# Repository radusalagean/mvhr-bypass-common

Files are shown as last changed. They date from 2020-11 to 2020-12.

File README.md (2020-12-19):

# MVHR Bypass

IOT device able to control the [MVHR Summer Bypass](https://www.zehnder.co.uk/summer-bypass) based on inside and outside temperatures.

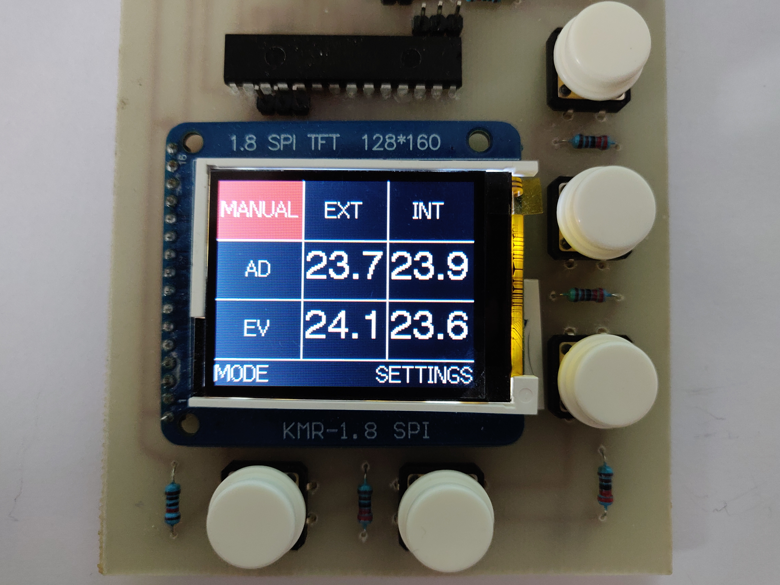
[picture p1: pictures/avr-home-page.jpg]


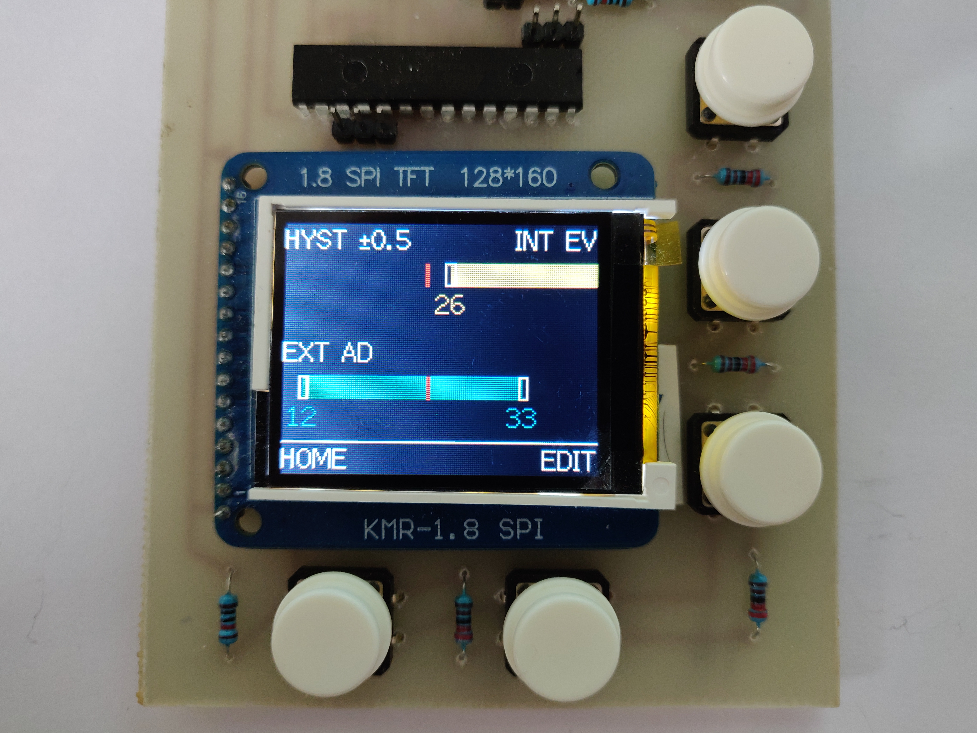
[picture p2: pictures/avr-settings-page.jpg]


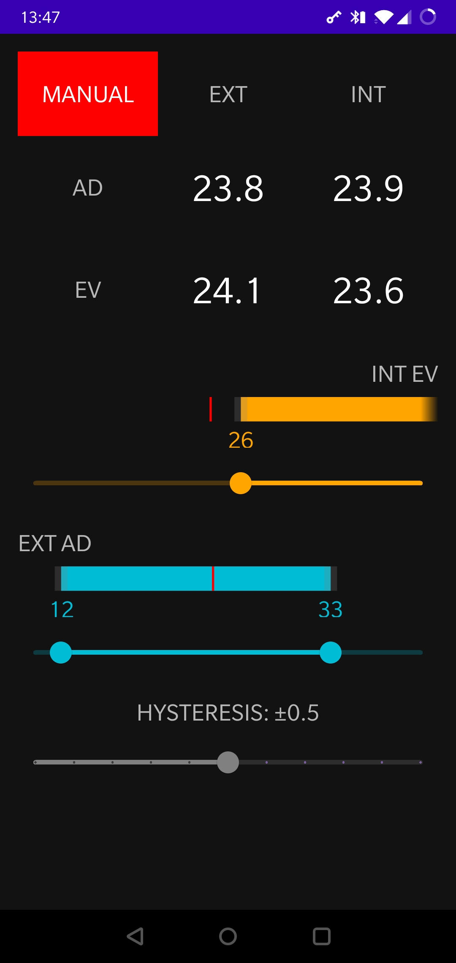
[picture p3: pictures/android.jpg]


## Compilation

Both the [**mvhr-bypass-arduino**](https://github.com/radusalagean/mvhr-bypass-arduino) and the [**mvhr-bypass-esp8266**](https://github.com/radusalagean/mvhr-bypass-esp8266) projects can be edited and compiled with **VSCode**, which needs the **Arduino IDE** installed and the following **VSCode plugins**:

- [Arduino](https://marketplace.visualstudio.com/items?itemName=vsciot-vscode.vscode-arduino)
- [C/C++](https://marketplace.visualstudio.com/items?itemName=ms-vscode.cpptools)

### Dependencies and versions

Check the **release notes** for each MVHR Bypass repo for the latest dependency versions known to work with that specific release.

In addition, the  **mvhr-bypass-arduino** project relies on the [**TFT_ILI9163**](https://github.com/radusalagean/TFT_ILI9163) library, which is included as a git submodule.

The **mvhr-bypass-common** repository contains code which is shared by both **mvhr-bypass-arduino** and **mvhr-bypass-esp8266** and is included in those repos as a git submodule.

### Software version compatibility

Add a new entry every time a new version is released. New releases go on top.

| [mvhr-bypass-arduino](https://github.com/radusalagean/mvhr-bypass-arduino) | [TFT_ILI9163](https://github.com/radusalagean/TFT_ILI9163) | [mvhr-bypass-esp8266](https://github.com/radusalagean/mvhr-bypass-esp8266) | [mvhr-bypass-common](https://github.com/radusalagean/mvhr-bypass-common) | [mvhr-bypass-android](https://github.com/radusalagean/mvhr-bypass-android) |
| --- | --- | --- | --- | --- |
| [1.0.0](https://github.com/radusalagean/mvhr-bypass-arduino/releases/tag/v1.0.0) | [1.0.0](https://github.com/radusalagean/TFT_ILI9163/releases/tag/v1.0.0) | [1.0.0](https://github.com/radusalagean/mvhr-bypass-esp8266/releases/tag/v1.0.0) | [1.0.0](https://github.com/radusalagean/mvhr-bypass-common/releases/tag/v1.0.0) | [1.0.0](https://github.com/radusalagean/mvhr-bypass-android/releases/tag/v1.0.0) |

### Flashing software updates on ATmega328p

Available options:

1. [Flashing with a **USB to Serial converter**](https://youtu.be/Sww1mek5rHU?t=1800)

1. Using an **Arduino board as an ISP**:

    - Write the **ArduinoISP** sketch which is included with Arduino IDE (located in File -> Examples -> ArduinoISP)

    - Hook up the Arduino Uno to the ATmega328p *(Double check the sketch in case these change in future versions)*:

    | Arduino Uno Pin | ATmega328p Pin |
    | --------------- | -------------- |
    | D10             | RST            |
    | D11             | D11            |
    | D12             | D12            |
    | D13             | D13            |
    - In VSCode, select the **Arduino as ISP** programmer and then run the **Arduino: Upload Using Programmer** command.

### Flashing software updates on ESP8266

Available options:

1. **OTA Update:**
   
   - Have the PC connected to the **same network** as ESP8266
   - In VSCode, in `arduino.json`, set the `port` value to the current IP address of the ESP8266
   - Upload
2. **Direct Serial Flashing:**
   
   - On the Arduino board, hook up the **RST** pin to **GND** (this bypasses the onboard microcontroller so you can use just the built in USB to Serial functionality)
   
   - **Remove the two header jumpers** that allow the ESP8266 and the ATmega328p to communicate through serial
   
   - Hook up the Arduino board to the ESP8266:
   
     | Arduino Pin | ESP8266 Pin                      |
     | ----------- | -------------------------------- |
     | RX          | RX (through the voltage divider) |
     | TX          | TX                               |
   
   - Get the ESP8266 in **Program Mode**:
     - Press and hold the **ESP RST micro-switch**
     - Press and hold the **ESP PROG micro-switch**
     - Release the **ESP RST micro-switch**
     - Release the **ESP PROG micro-switch**
   - In VSCode, select the appropriate **Serial port**
   - Upload
   - Press the **ESP RST micro-switch** to reset to normal mode

### Receiving serial messages for debugging purposes

- On the Arduino board, hook up the **RST** pin to **GND**

- For the **ATmega328p**, hook up:

  | Arduino Pin | ATmega328p Pin |
  | ----------- | -------------- |
  | TX          | TX             |
  
- For the **ESP8266**, hook up:

  | Arduino Pin | ESP8266 Pin |
  | ----------- | ----------- |
  | TX          | Serial1 TX  |

- Open the **Serial Monitor** and set the baud rate to **9600 bps**

## Hardware

- 1x 2 pin screw connector
- 1x 6 pin screw connector (or 2x 3 pin)
- 1x AMS1117 module (3.3 V)
- 1x 10 µF capacitor
- 1x ATmega328P-PU
- 2x 22 pF capacitors
- 1x 16 MHz crystal
- 1x ESP8266-01 (labeled "AI-Cloud inside")
- 5x push buttons (4 pin)
- 2x micro-switches (2 pin)
- 2x header jumpers (2 pin)
- 11x header pins
- 1x ILI9163 1.8" SPI TFT 128*160 (labeled "KMR-1.8 SPI")
- 1x 47 Ω resistor
- 1x 1 kΩ resistor
- 1x 2 kΩ resistor
- 9x 2.2 kΩ resistor
- 5x 3.3 kΩ resistor
- 1x 4.7 kΩ resistor
- 5x 10 kΩ resistor
- 1x Relay (5 V)
- 4x DS18B20 Temperature sensors

### PCB

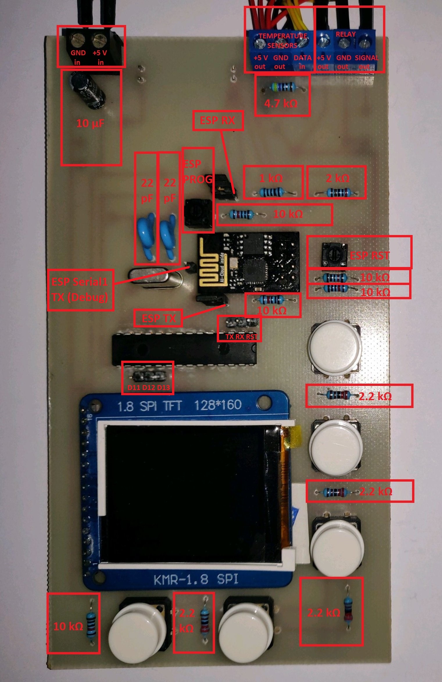
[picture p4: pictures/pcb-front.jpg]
PCB Front


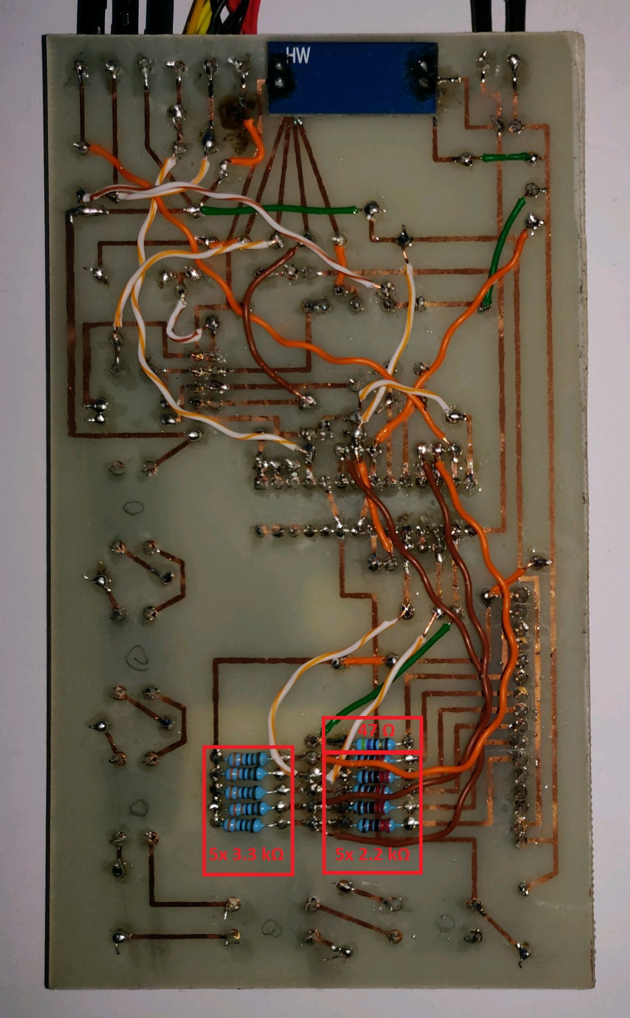
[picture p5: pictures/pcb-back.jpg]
PCB Back


### Wiring

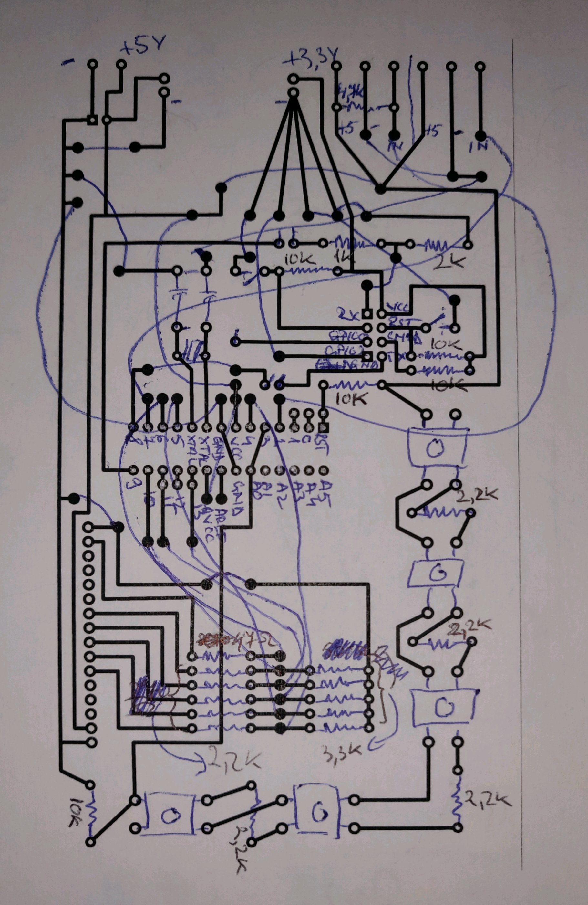
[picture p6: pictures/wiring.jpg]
Wiring


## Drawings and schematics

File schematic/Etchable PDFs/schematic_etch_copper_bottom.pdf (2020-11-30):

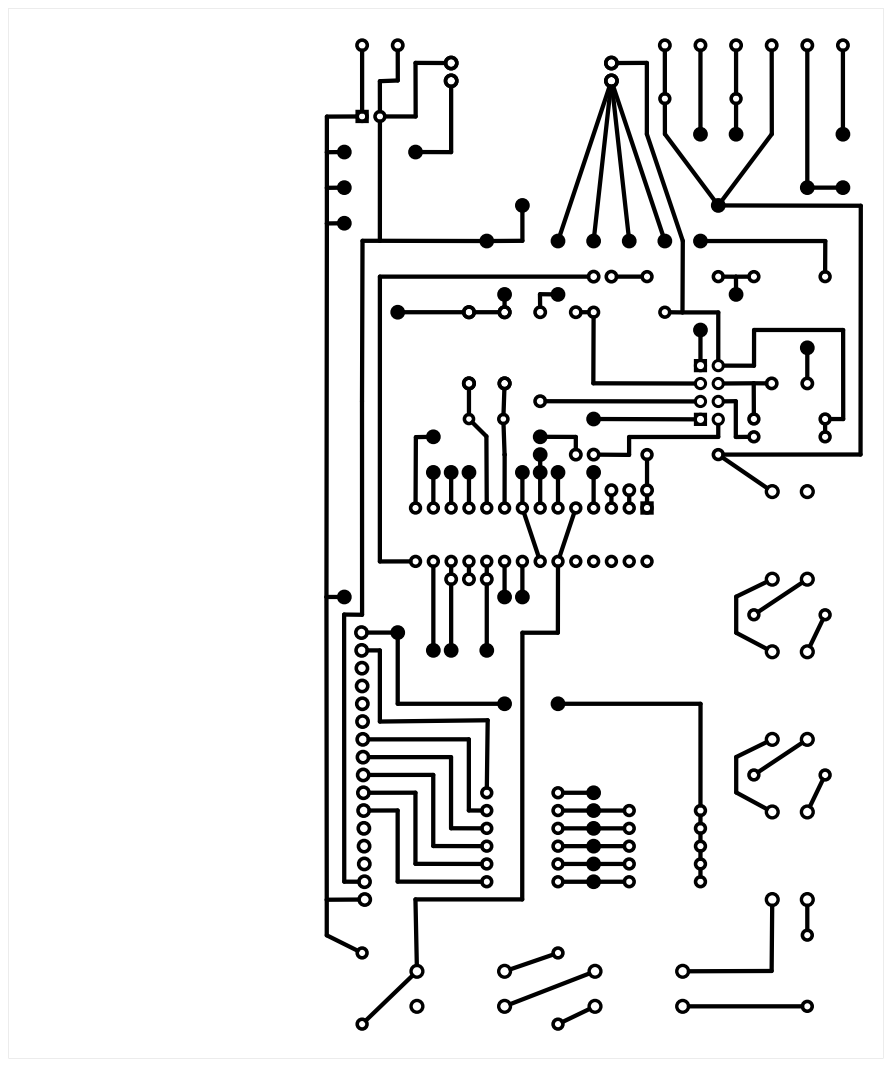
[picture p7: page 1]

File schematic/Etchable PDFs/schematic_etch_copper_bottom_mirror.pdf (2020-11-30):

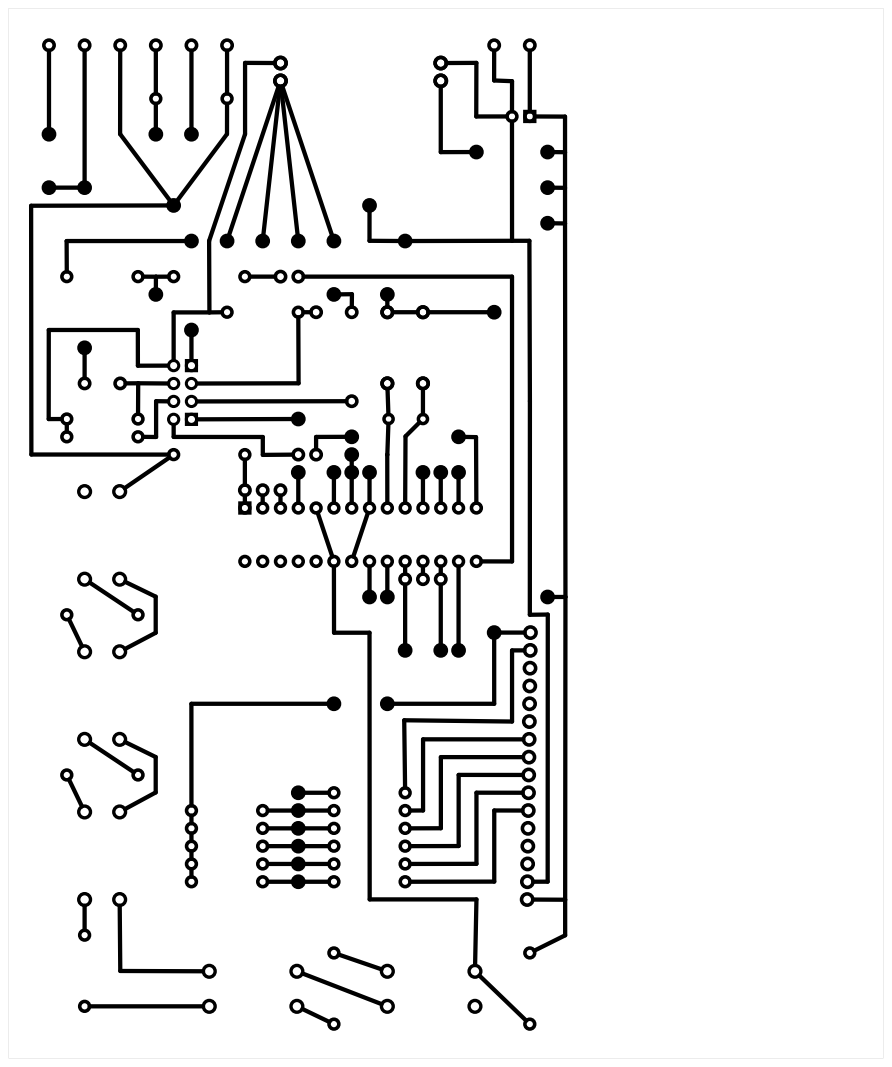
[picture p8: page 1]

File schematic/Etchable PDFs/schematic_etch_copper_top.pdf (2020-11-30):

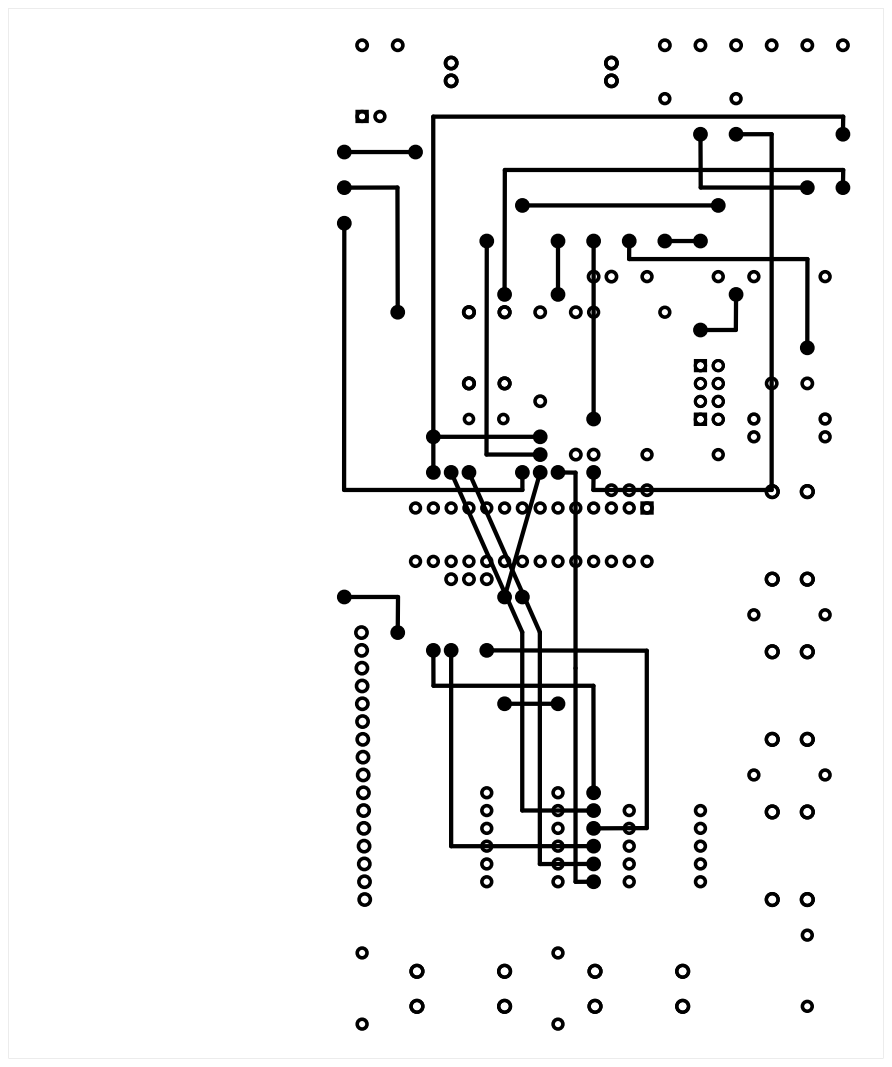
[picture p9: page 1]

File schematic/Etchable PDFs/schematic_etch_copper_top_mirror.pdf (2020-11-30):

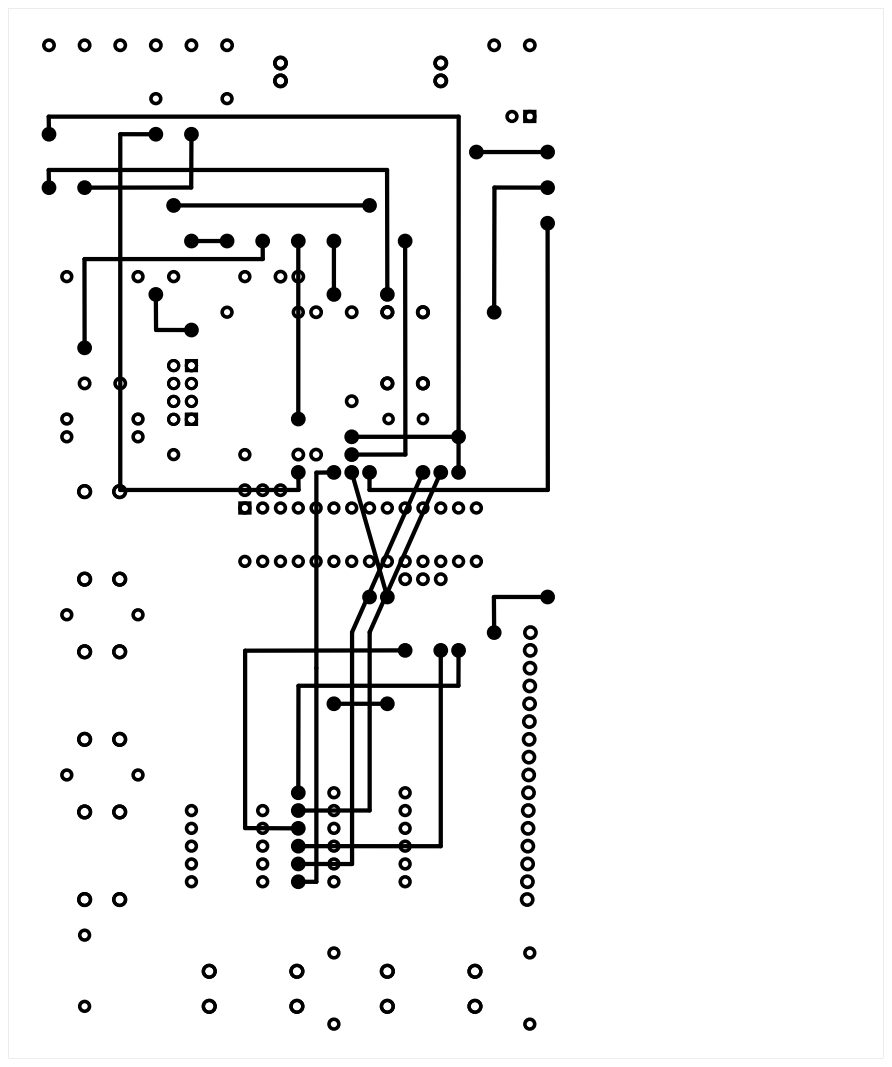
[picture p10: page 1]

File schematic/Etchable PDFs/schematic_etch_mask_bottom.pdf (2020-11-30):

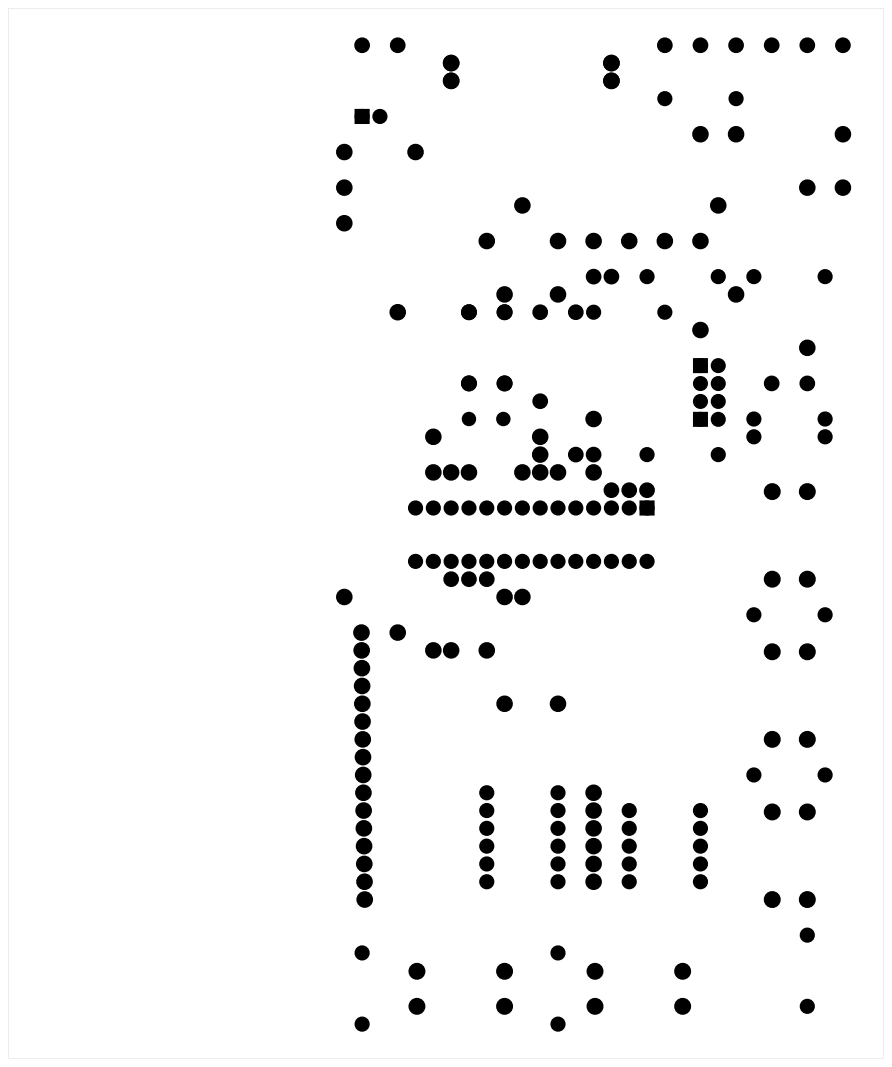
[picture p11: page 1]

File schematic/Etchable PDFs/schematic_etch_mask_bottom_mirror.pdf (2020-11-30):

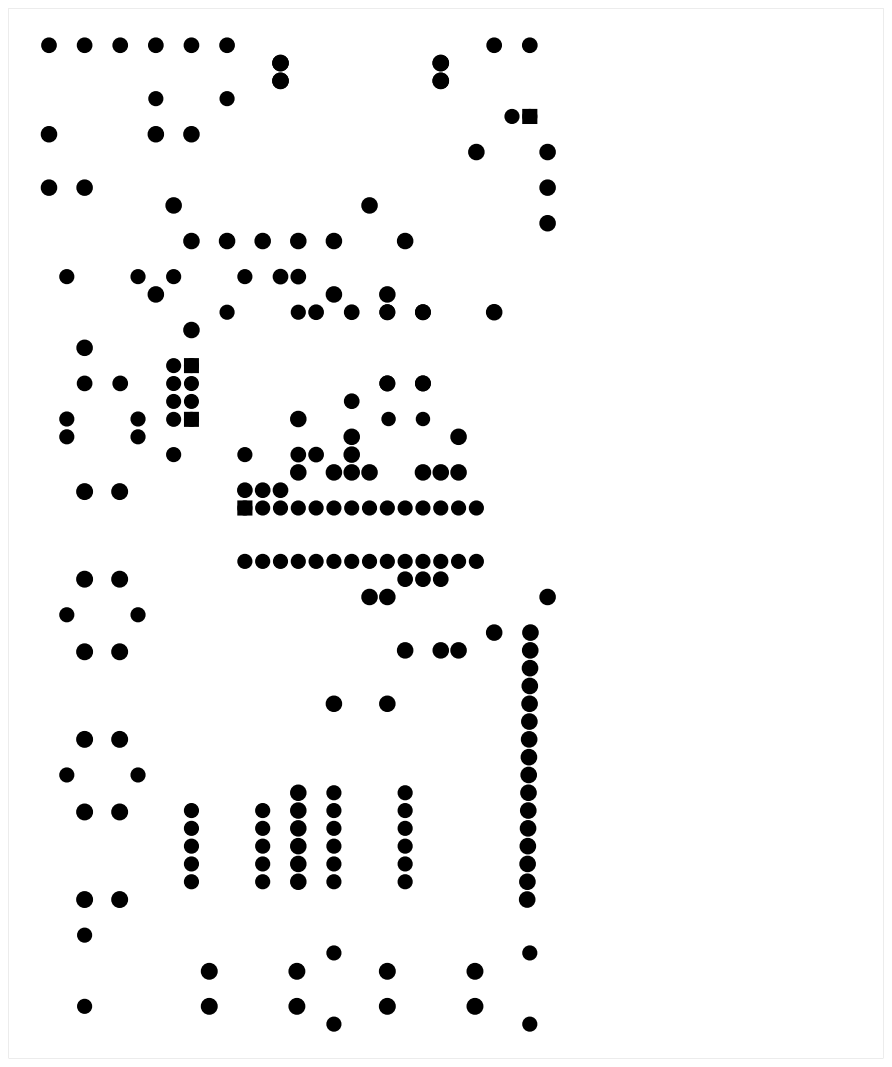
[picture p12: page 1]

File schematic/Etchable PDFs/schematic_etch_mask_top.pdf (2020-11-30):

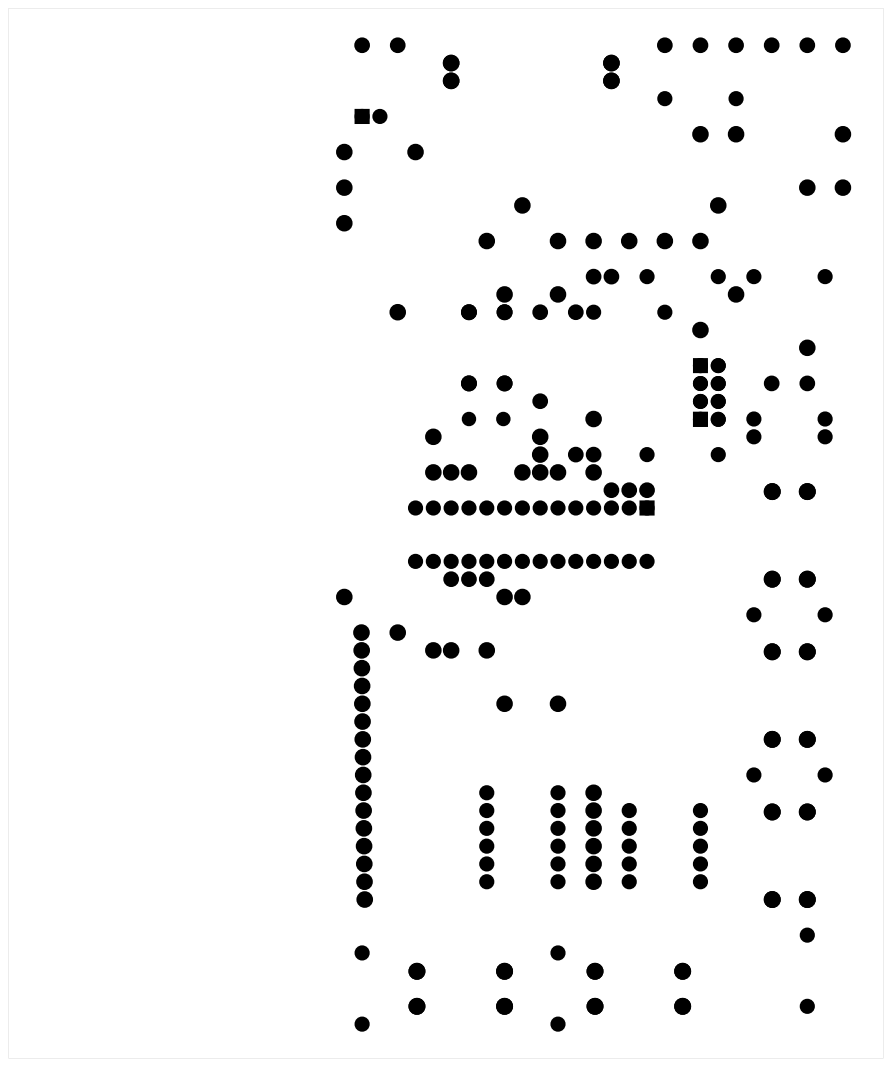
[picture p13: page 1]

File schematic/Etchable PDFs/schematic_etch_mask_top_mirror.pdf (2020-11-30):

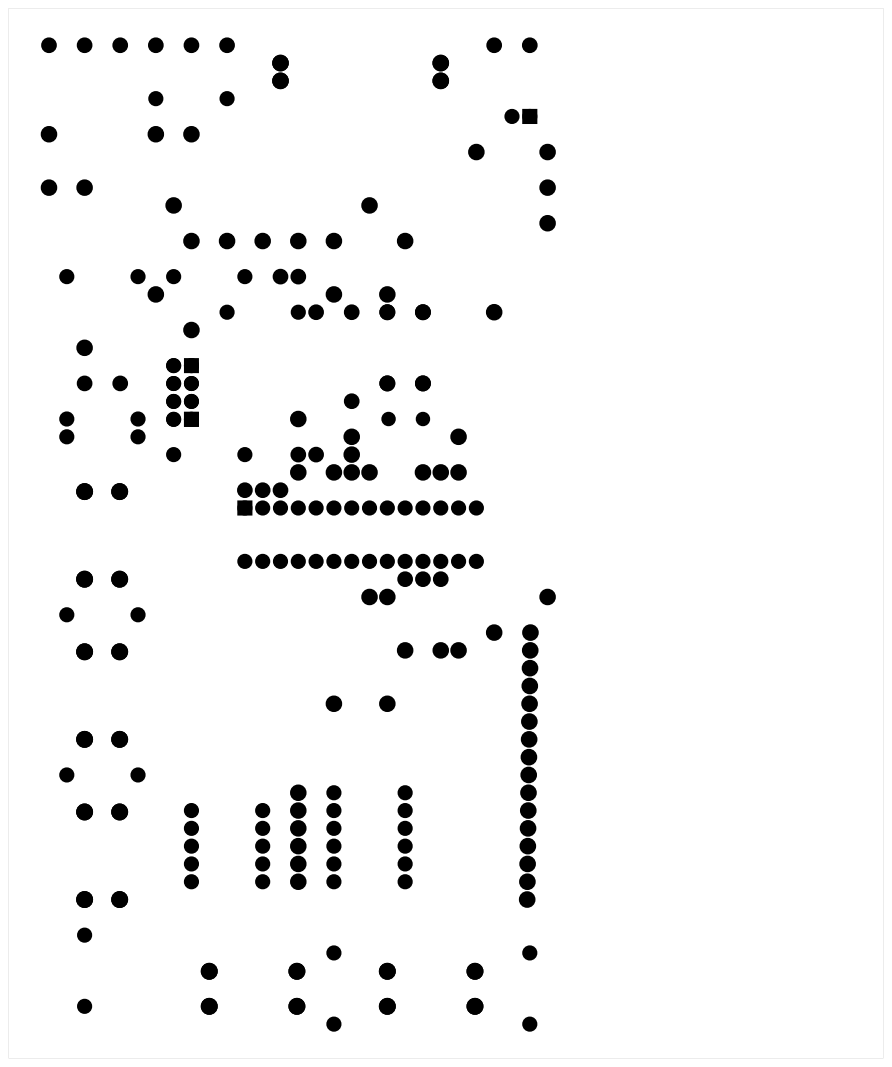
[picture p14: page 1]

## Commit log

2020-11-23 Print(ln) char support
2020-11-23 Add support for all print(ln) methods in the base wrapper
2020-11-23 Bugfix: Don't wait for more bytes in last stage
2020-11-25 Update contract for Init Data and Temperatures exchange
2020-11-25 Added data model for Temperatures and InitData
2020-11-30 Schematic (milestone 1 - wip)
    [schematic.fzz]
2020-11-30 Schematc - part 2
    [schematic.fzz]
2020-11-30 Schematic EOD Nov 30 2020
    [schematic.fzz]
2020-12-16 Local Contract code (apply state temperatures request)
